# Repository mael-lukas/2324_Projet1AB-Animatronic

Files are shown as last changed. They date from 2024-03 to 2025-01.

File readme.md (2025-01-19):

# DEA : Dynamic Eagle Animatronic

Depuis la Grêce antique et le mythe du géant de bronze Talos les hommes ont toujours cherchés à créer des automates avec les moyens à leur disposition. Les animatroniques sont l'achèvement actuel de ce désir. Ce sont des poupées mécaniques plus ou moins réalistes dont le fonctionnement interne fait intervenir autant de la mécanique que de l'électronique.
Elles sont depuis plusieurs décennies et encore aujourd'hui principalement utilisées dans le domaine du divertissement au travers des parcs d'attraction, des films et des séries.

Dans le cadre d'un projet de 1ère année à l'école d'ingénieur ENSEA supervisé par [M.Papazoglou](https://github.com/mael-lukas/2324_Projet1AB_Animatronic/tree/main#supervis%C3%A9-par-mpapazoglou) nous allons créer créer une animatronique d'aigle en 10 séances de 4h. Cet animatronic sera
capable d'ouvrir et de rabattre ses ailes, d'ouvrir et de fermer ses paupières, d'ouvrir et de fermer son bec, de pivoter sa tête (optionnel). Ces mouvements seront commandés par
l'appui de différents boutons.

<table>
  <tr>
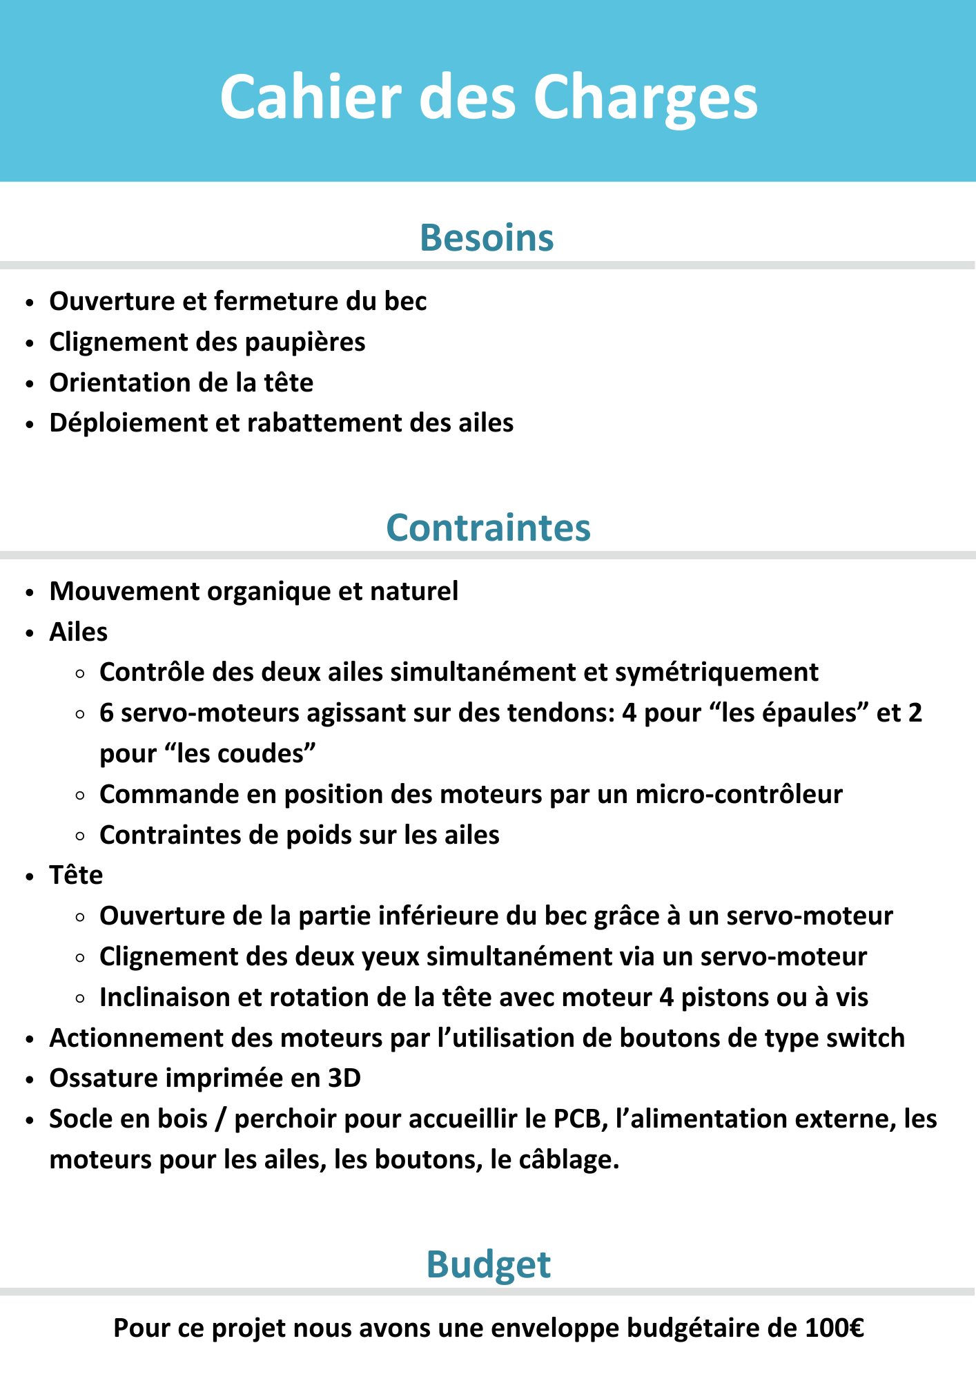
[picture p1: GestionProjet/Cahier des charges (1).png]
Cahier des charges
    <td></td>
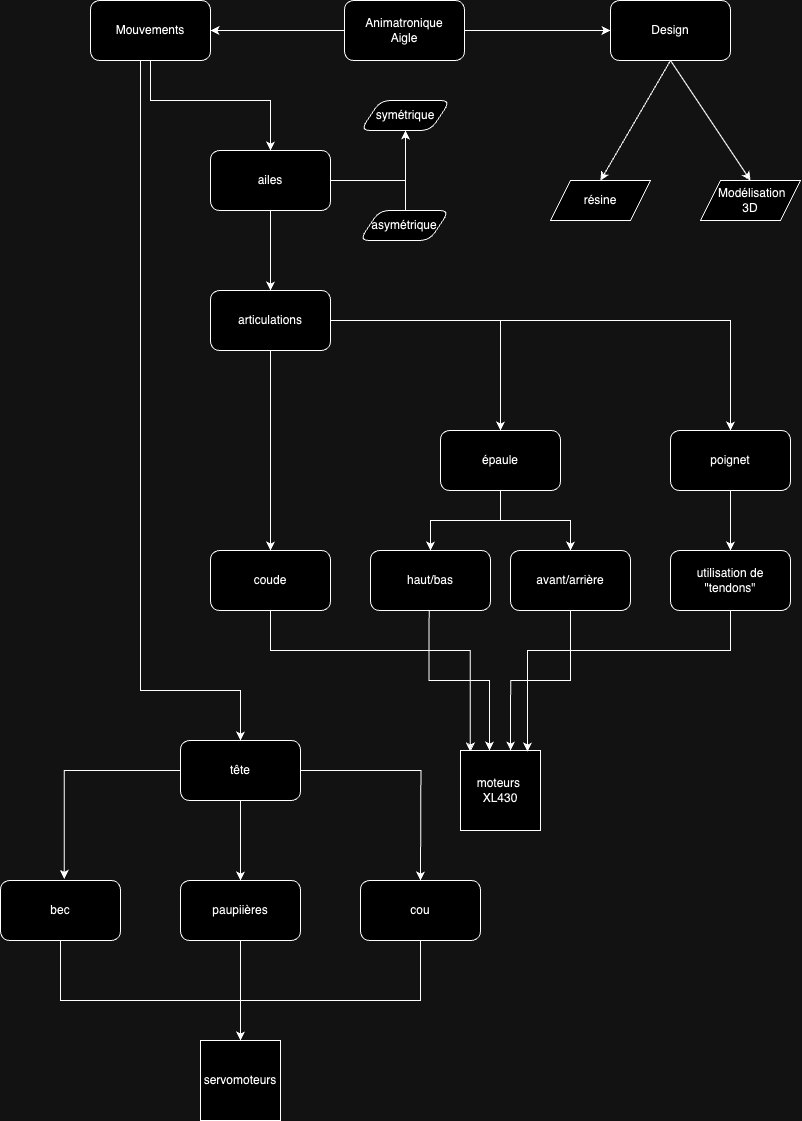
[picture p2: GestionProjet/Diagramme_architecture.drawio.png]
Diagramme d'architecture
    <td></td>
  </tr>
</table>

  [](https://github.com/mael-lukas/2324_Projet1AB_Animatronic/blob/main/GestionProjet/Cahier%20des%20charges%20(1).png)    
  [](https://github.com/mael-lukas/2324_Projet1AB_Animatronic/blob/main/GestionProjet/Diagramme_architecture.drawio.png)

# Equipe
Membres de l'équipe : 
* #### Vincent Fernandes
    * [Github](https://github.com/FernandesVincent)
    * [Linkedin](https://www.linkedin.com/in/vincent-fernandes-0981552a6/)
* #### Maël Lukas
    * [Github](https://github.com/mael-lukas)
    * [Linkedin](https://www.linkedin.com/in/mael-lukas/)
* ##### Romane Ponthieu
    * [Github](https://github.com/Romanepnth)
    * [Linkedin](https://www.linkedin.com/in/romane-ponthieu/)
* #### Marie Ceccaldi
    * [Github](https://github.com/mariececcaldi1)
    * [Linkedin](https://www.linkedin.com/in/marie-ceccaldi-887616300/)
* #### Sedrenn Labrousse
    * [Github](https://github.com/Sedrennl)
    * [Linkedin](https://www.linkedin.com/in/sédrenn-labrousse-24b2a5295/)

* #### Supervisé par Nicolas Papazoglou
    * [Github](https://github.com/DBXYD?tab=overview&from=2024-05-01&to=2024-05-29)
    * [Linkedin](https://www.linkedin.com/in/nicolas-papazoglou-38382646/?originalSubdomain=fr)

# Journal de bord

## Séance 1
   Cette séance, étant la première, nous a servit à définir notre projet au travers de la création d'une première version d'un cahier des charges et d'un diagramme d'architecture. Afin de nous organiser au mieux au vu du temps disponible à la création de ce projet nous nous sommes directement répartit différentes tâches à réaliser durant les semaines qui suivent.
   * #### modélisation 3D de l'aigle
        * [Sedrenn](https://github.com/mael-lukas/2324_Projet1AB_Animatronic/tree/main?tab=readme-ov-file#sedrenn-labrousse)
   * #### programmation des moteurs
        * [Maël](https://github.com/mael-lukas/2324_Projet1AB_Animatronic/tree/main?tab=readme-ov-file#ma%C3%ABl-lukas)
   * #### création des différents PCB
        * [Romane](https://github.com/mael-lukas/2324_Projet1AB_Animatronic/tree/main?tab=readme-ov-file#romane-ponthieu)
        * [Marie](https://github.com/mael-lukas/2324_Projet1AB_Animatronic/tree/main?tab=readme-ov-file#marie-ceccaldi)
        * [Vincent](https://github.com/mael-lukas/2324_Projet1AB_Animatronic/tree/main?tab=readme-ov-file#vincent-fernandes)

## Séance 2
   Durant cette séance nous avons affiné notre cahier des charges et notre diagramme d'architecture disponible ci-dessous:

   Nous en avons déduis la nécessité d'avoir un minimum de 2 PCB afin de réaliser notre animatronique, le principal qui contiendrait le microprocesseur ainsi que différents connectiques tandis que le secondaire incorporerai principalement en son sein tout les régulateurs de tension nécessaire à l'actionnment des moteurs. [PCB](https://github.com/mael-lukas/2324_Projet1AB_Animatronic?tab=readme-ov-file#pcb)
   Pendant ce temps, [Sedrenn](https://github.com/mael-lukas/2324_Projet1AB_Animatronic/tree/main?tab=readme-ov-file#sedrenn-labrousse) et [Maël](https://github.com/mael-lukas/2324_Projet1AB_Animatronic/tree/main?tab=readme-ov-file#ma%C3%ABl-lukas)
 se sont chargés de la commande des différents composants dont nous ne disposions pas à l'école.
   
## Séance 3
   À cette étape du projet nous avons choisis de créer un nouveau [PCB](https://github.com/mael-lukas/2324_Projet1AB_Animatronic/tree/main?tab=readme-ov-file#yeux) dans le but de pouvoir placer les LED RGB au plus proches des yeux de d'aigle. Ce PCB sera donc utilisé deux fois, un pour chaque oeil.
   En parallèle à cela, nous nous sommes penchés sur la réalisation d'un socle dont le but est d'accueillir le [PCB principal](https://github.com/mael-lukas/2324_Projet1AB_Animatronic/tree/main?tab=readme-ov-file#corps) ainsi que l'alimentation tout en permettant de poser l'aigle sur celui-ci pour y connecter l'ensemble des câbles.
   
## Séance 4
   Cette séance a permis la finalisation des schematic des 3 [PCB](https://github.com/mael-lukas/2324_Projet1AB_Animatronic?tab=readme-ov-file#pcb) crées sous Kicad et ainsi le passage à l'étape PCB editor pour les membres affectés à cette partie du projet.
   Pendant ce temps [Maël](https://github.com/mael-lukas/2324_Projet1AB_Animatronic/tree/main?tab=readme-ov-file#ma%C3%ABl-lukas) a finalisé une première version du code des petits moteurs et [Sedrenn](https://github.com/mael-lukas/2324_Projet1AB_Animatronic/tree/main?tab=readme-ov-file#sedrenn-labrousse) a trouvé le modèle 3D d'un aigle qui servira de base pour notre projet.

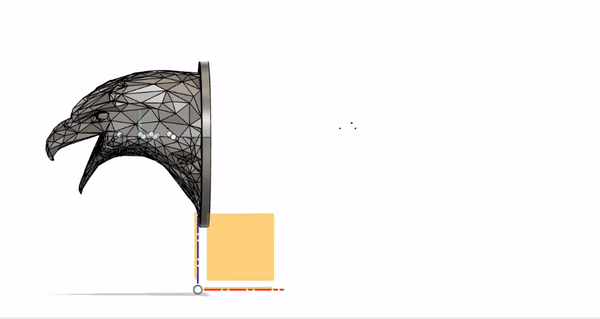
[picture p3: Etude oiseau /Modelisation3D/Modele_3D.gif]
Modèle 3D

   
## Séance 5
   Au cours de ces 4 heures M.Papazoglou a pu vérifier les 3 [PCB](https://github.com/mael-lukas/2324_Projet1AB_Animatronic?tab=readme-ov-file#pcb) et nous faire des retours pour que l'on puisse faire les dernières retouches pour ensuite pouvoir passer la commande.
   
   À ce moment là dans l'avancée du projet, toutes les réalisations énoncées à la séance 1 ont pu avancer comme il ce doit. Les pcb étaient en phase de finalisation, la programmation des moteurs a permis la commande d'un petit moteur tandis que les moteurs XL430 voyaient leur fichiers header être terminés. Finalement, la modélisation 3D...

## Séance 6
   Au cours de cette séance nous avons reçu les commandes de composants faites durant la séance 2 ainsi que les PCB qui ont donc pu être soudés par [Marie](https://github.com/mael-lukas/2324_Projet1AB_Animatronic/tree/main?tab=readme-ov-file#marie-ceccaldi) et [Romane](https://github.com/mael-lukas/2324_Projet1AB_Animatronic/tree/main?tab=readme-ov-file#romane-ponthieu) durant ces 4 heures.
   En parralèle à cela, [Sedrenn](https://github.com/mael-lukas/2324_Projet1AB_Animatronic/tree/main?tab=readme-ov-file#sedrenn-labrousse) a finalisée la première version de la tête de l'aigle en y incluant les moteurs et PCB associés:
   
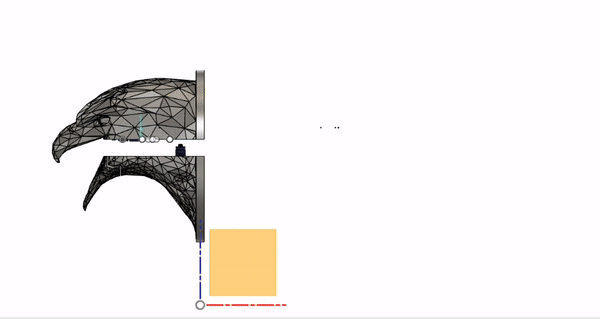
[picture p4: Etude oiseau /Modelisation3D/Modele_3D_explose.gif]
Modèle 3D finalisé

   
   [Vincent](https://github.com/mael-lukas/2324_Projet1AB_Animatronic/tree/main?tab=readme-ov-file#vincent-fernandes), quant à lui, à réalisé un premier prototype du socle réfléchit à la [Séance 3](https://github.com/mael-lukas/2324_Projet1AB_Animatronic?tab=readme-ov-file#s%C3%A9ance-3)
   
## Séance 7
   Durant cette séance, [Marie](https://github.com/mael-lukas/2324_Projet1AB_Animatronic/tree/main?tab=readme-ov-file#marie-ceccaldi) et [Romane](https://github.com/mael-lukas/2324_Projet1AB_Animatronic/tree/main?tab=readme-ov-file#romane-ponthieu) ont crées le modèle 3D d'un cache pour l'alimentation: 
   
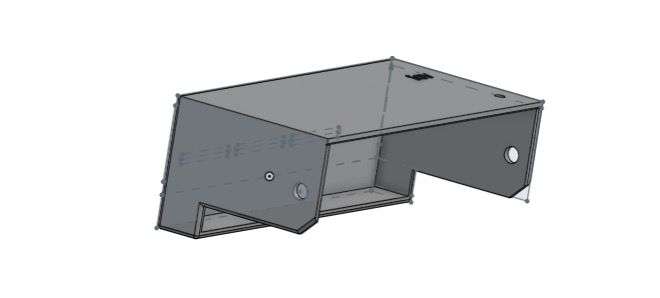
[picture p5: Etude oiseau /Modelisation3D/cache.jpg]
cache
   
   
   Pendant ce temps [Sedrenn](https://github.com/mael-lukas/2324_Projet1AB_Animatronic/tree/main?tab=readme-ov-file#sedrenn-labrousse) a imprimée une première version de la tête de l'aigle. [Vincent](https://github.com/mael-lukas/2324_Projet1AB_Animatronic/tree/main?tab=readme-ov-file#vincent-fernandes), pour sa part, a entammé la rédaction du fichier readme.md en markdown et en HTML.
   
## Séance 8
   Au cours de cette séance, [Marie](https://github.com/mael-lukas/2324_Projet1AB_Animatronic/tree/main?tab=readme-ov-file#marie-ceccaldi) et [Romane](https://github.com/mael-lukas/2324_Projet1AB_Animatronic/tree/main?tab=readme-ov-file#romane-ponthieu) ont finalisées le modèle 3D du cache entammé à la séance précédente, puis l'ont [imprimé](https://github.com/mael-lukas/2324_Projet1AB_Animatronic/blob/main/Hardware/PCB/screenshots/picture%20cache.jpg).

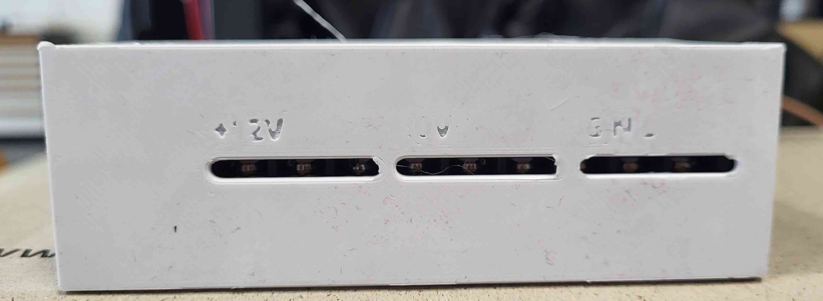
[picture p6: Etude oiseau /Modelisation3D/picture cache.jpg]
cache


Au même moment [Maël](https://github.com/mael-lukas/2324_Projet1AB_Animatronic/tree/main?tab=readme-ov-file#ma%C3%ABl-lukas) a mis au propre [l'architecture du code](https://github.com/mael-lukas/2324_Projet1AB_Animatronic?tab=readme-ov-file#code)
   
## Séance 9
  Durant cette séance nous avons réalisé une première présentation orale du projet DEA. De plus, nous avons eu les impression 3D des nouvelles et dernières versions du cache de l'alimentation ainsi que de la tête de l'aigle, toutes deux présentées ci-dessous:

<table>
  <tr>
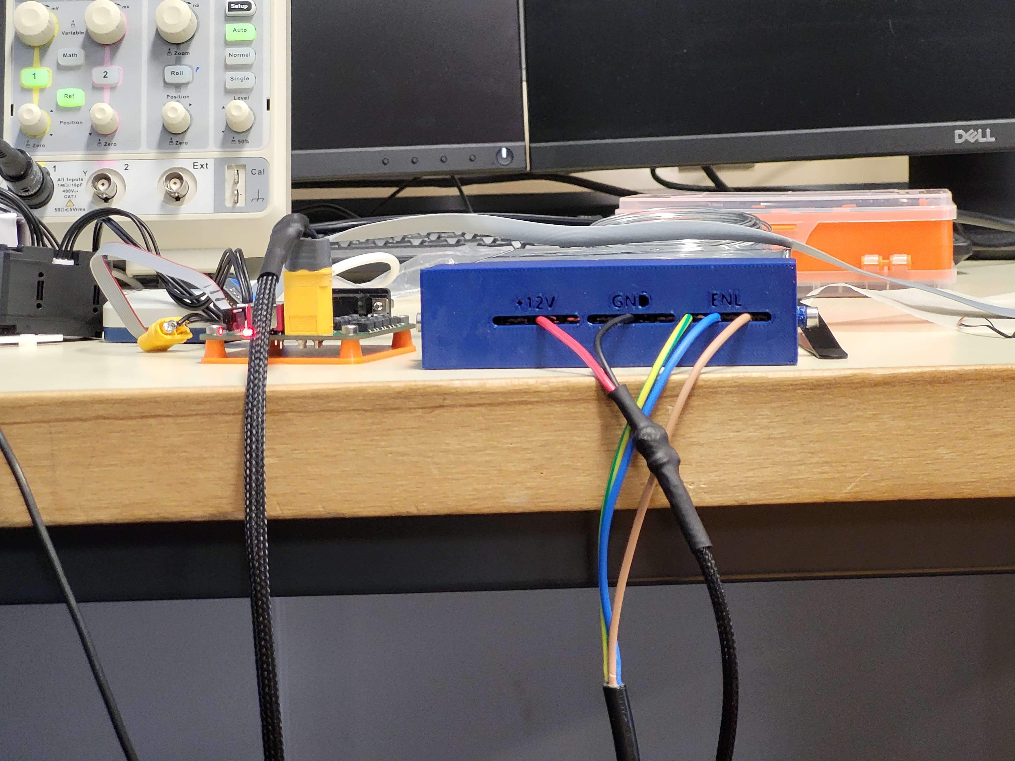
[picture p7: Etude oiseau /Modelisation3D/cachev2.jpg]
cachev2
    <td></td>
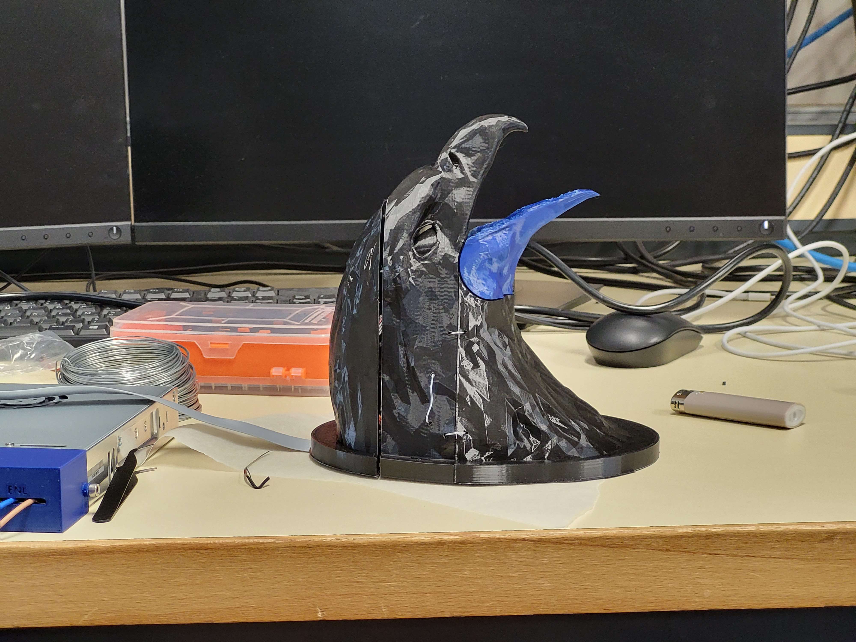
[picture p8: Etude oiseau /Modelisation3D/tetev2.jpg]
tetev2
    <td></td>
  </tr>
</table>
  
## Séance 10
   
   Au cours de cette dernière séance, nous avons assemblé la tête de l'aigle avec les différents PCB crée au cours des séance précédentes afin de permettre une ouverture et une fermeture du bec ainsi que le mouvement des paupières, ce que nous avons réussi comme en témoigne [la vidéo de démonstration du projet](https://github.com/mael-lukas/2324_Projet1AB_Animatronic/tree/main?tab=readme-ov-file#rendu-final).

   Pour faire un bilan de ce projet revenons à la base de celui-ci et comparons le à notre rendu final. Au début du projet notre objectif était de réaliser un animatronique d'aigle capable de différents mouvements de la tête ainsi que des ailes, cependant dans notre [rendu final](https://github.com/mael-lukas/2324_Projet1AB_Animatronic/tree/main?tab=readme-ov-file#rendu-final) nous avons seulement réussi à avoir la tête dans laquelle le bec et la paupière bougent. Cette différence s'explique par la difficulté liée à l'ambition d'un tel projet, en effet il y a eu plusieurs difficultés dans ce projet tel que des problèmes au niveau des PCB (problèmes de soudure, d'inversion de placement de SDA et SLC entre deux PCB et autres) ou encore sur la création de librairies pour la partie programmation et des modélisations 3D qui ont nécessitées plusieurs versions pour être opérationnelles. 
   Malgré tout cela, l'ensemble du groupe est fier et heureux d'avoir réussi à obtenir ce [résultat](https://github.com/mael-lukas/2324_Projet1AB_Animatronic/tree/main?tab=readme-ov-file#rendu-final) et ce projet ne s'arrête pas ici puisque, en effet, le groupe dans son ensemble a décidé de poursuivre ce projet durant la deuxième année de notre cursus afin de finir ce qui était prévu initialement. 
   Cependant, nous avons décidé de ne pas nous arrêter à ce que nous avions prévu et nous commencons déjà à réfléchir à des améliorations pour le DEA tel que:
   1. Un speaker dans le bec de l'aigle lié à un capteur de distance pour changer ce que l'aigle dit en fonction de la distance avec son interlocuteur.
   2. Un système permettant de contrôler les mouvements de l'aigle en fonction des mouvement de la main de l'utilisateur.
   3. Une application permettant de changer la vitesse des moteurs, la couleur des LED des yeux et de jouer certaines séquences de mouvement de l'aigle.

Ces idées ne sont encore que des réflexions et seront amennées a évoluées au cours de l'année qui arrive.
   
# Livrables
## PCB

#### Corps

Ce PCB est le PCB principal contenant le microprocesseur ainsi que les connecteurs et les bouttons utiles à l'utilisateur.

<table>
  <tr>
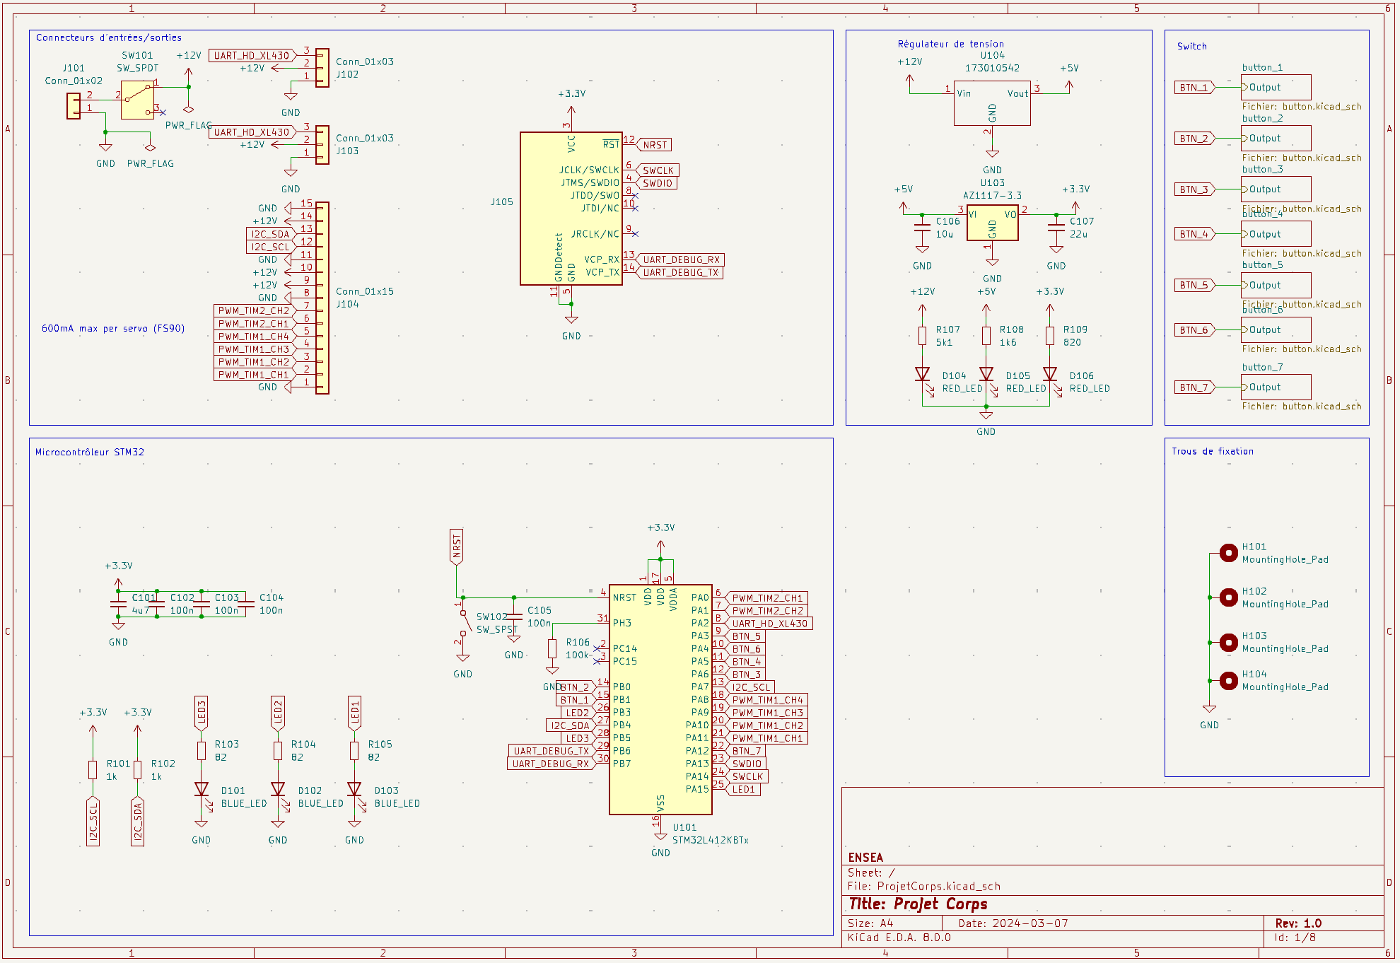
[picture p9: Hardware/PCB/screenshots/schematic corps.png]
schematic corps
    <td></td>
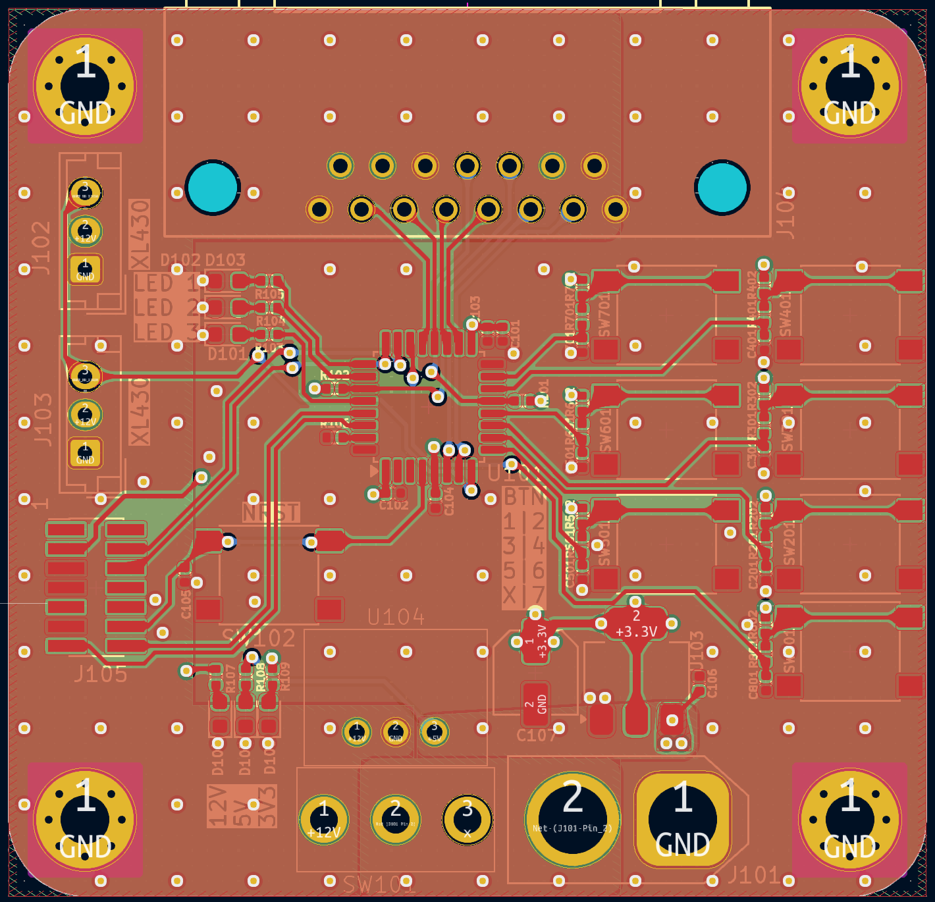
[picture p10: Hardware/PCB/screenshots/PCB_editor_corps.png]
PCB editor corps
    <td></td>
  </tr>
</table>

[Schematic](https://github.com/mael-lukas/2324_Projet1AB_Animatronic/blob/main/Hardware/PCB/screenshots/schematic%20corps.png)         
[PCB editor](https://github.com/mael-lukas/2324_Projet1AB_Animatronic/blob/main/Hardware/PCB/screenshots/PCB_editor_corps.png)

#### Tête

Ce PCB sert à réguler les tensions envoyées aux moteurs et contient également le LED driver qui permet de commander les LED présentes sur le [PCB des yeux](https://github.com/mael-lukas/2324_Projet1AB_Animatronic/tree/main?tab=readme-ov-file#yeux).

<table>
  <tr>
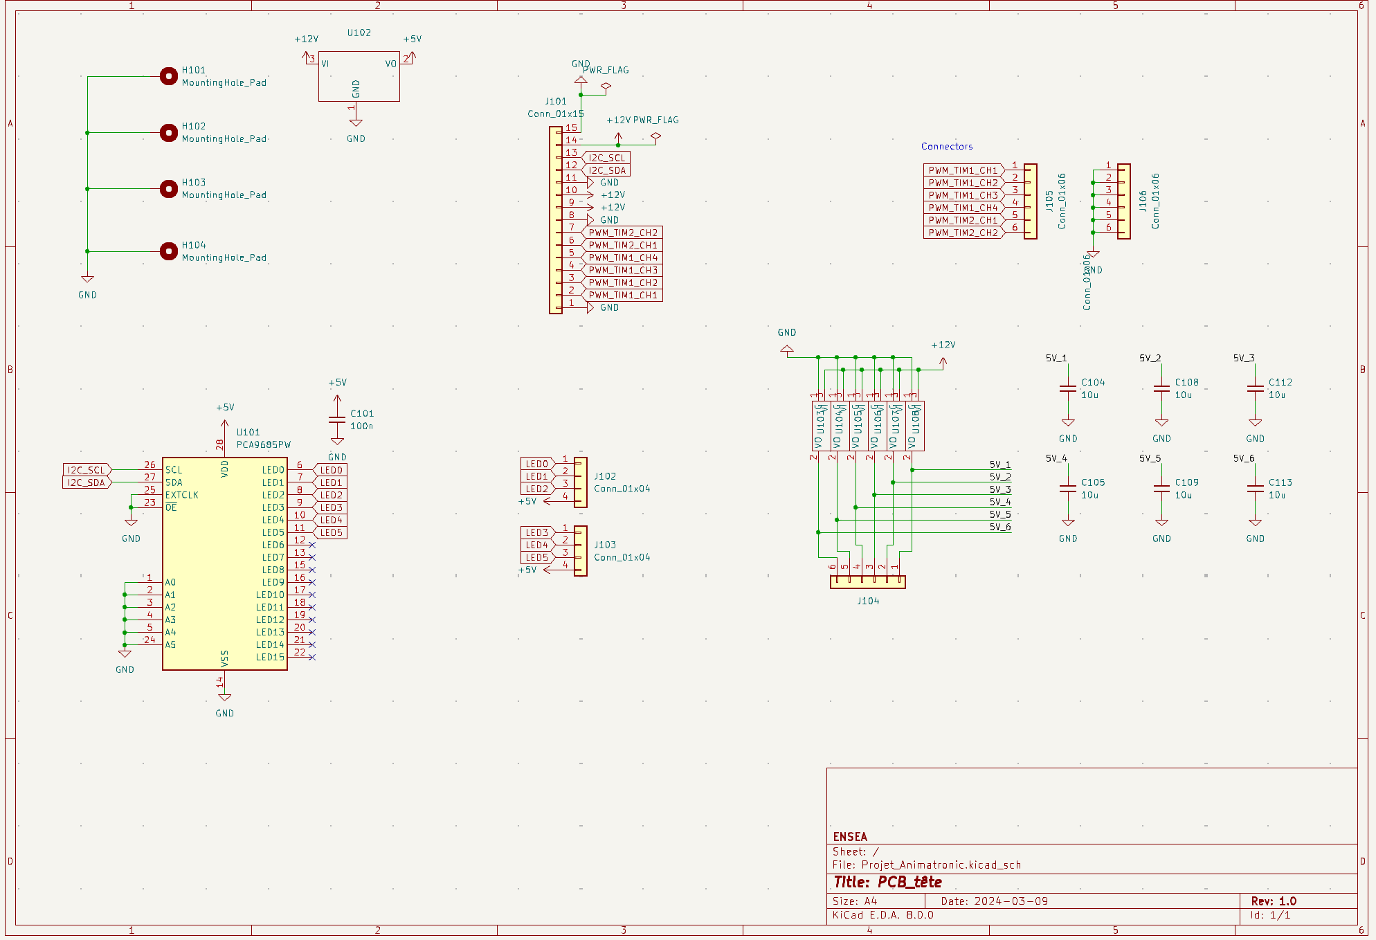
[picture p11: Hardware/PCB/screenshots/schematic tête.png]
schematic tête
    <td></td>
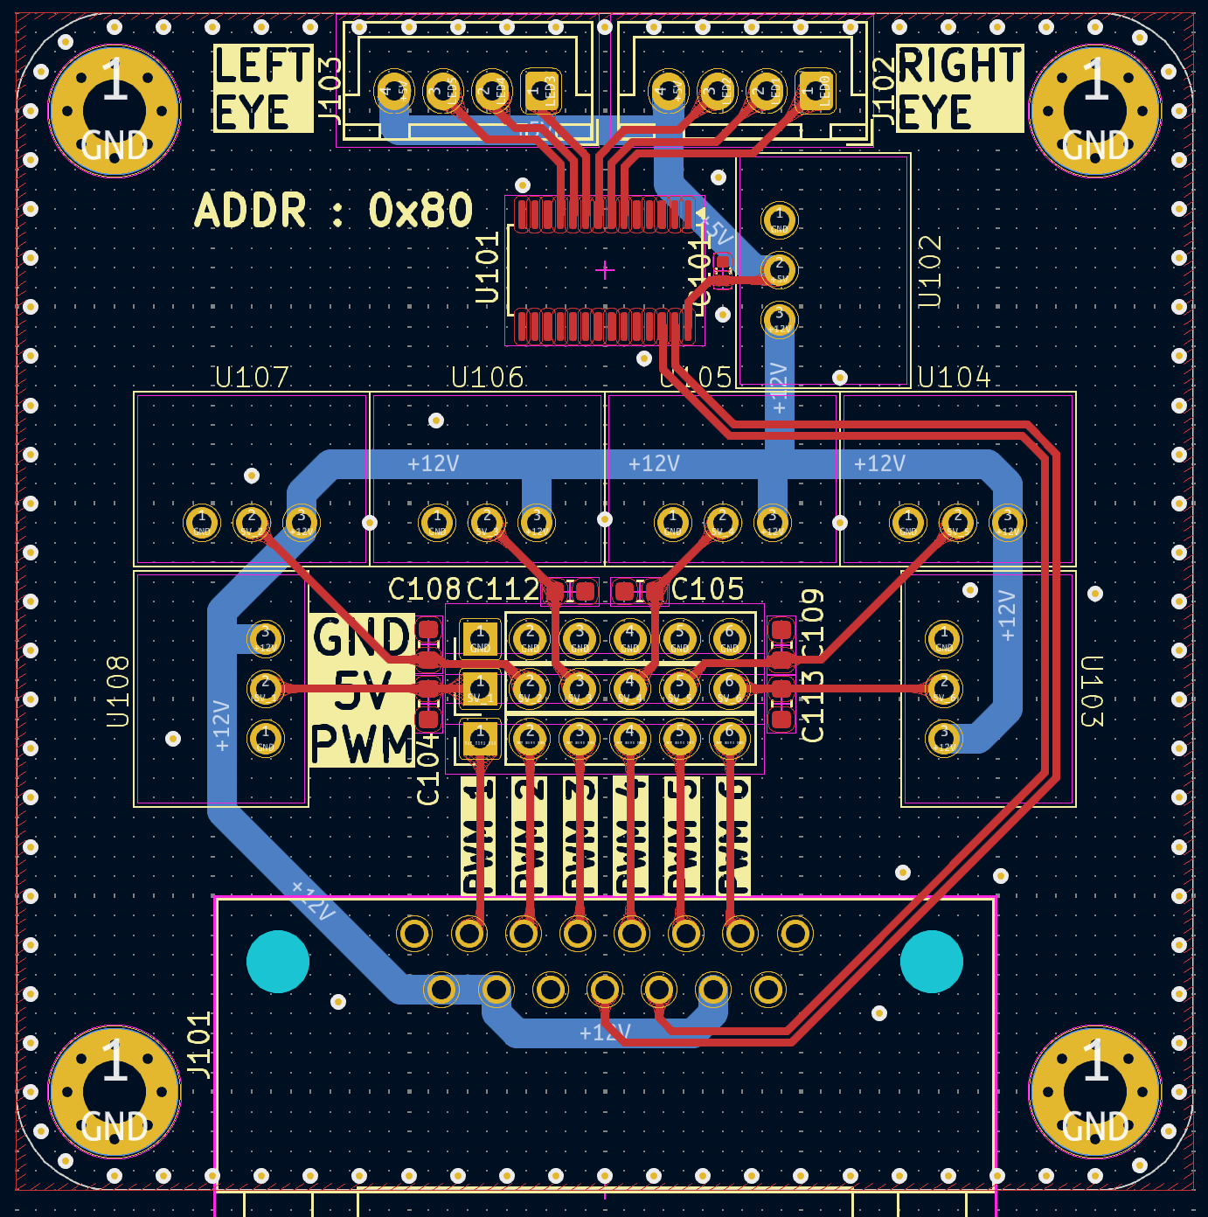
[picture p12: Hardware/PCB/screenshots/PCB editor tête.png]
PCB editor tête
    <td></td>
  </tr>
</table>

[Schematic](https://github.com/mael-lukas/2324_Projet1AB_Animatronic/blob/main/Hardware/PCB/screenshots/schematic%20t%C3%AAte.png)   
[PCB editor](https://github.com/mael-lukas/2324_Projet1AB_Animatronic/blob/main/Hardware/PCB/screenshots/PCB%20editor%20t%C3%AAte.png)

#### Yeux

Ce PCB, utilisé deux fois dans le DEA (un pour chaque oeil) à pour unique utilité de placer les LED au plus proche des yeux grâce à un connecteur qui le relie au [PCB de la tête](https://github.com/mael-lukas/2324_Projet1AB_Animatronic/tree/main?tab=readme-ov-file#t%C3%AAte).

<table>
  <tr>
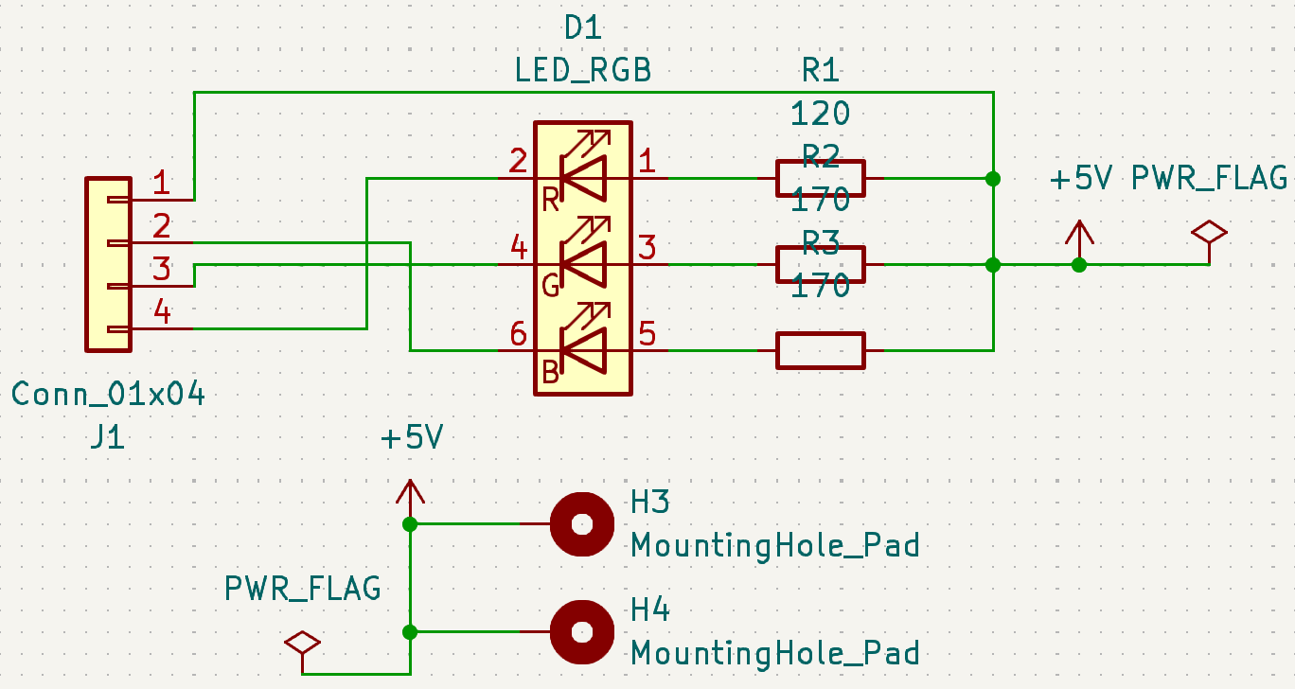
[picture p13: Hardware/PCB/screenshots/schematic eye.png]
schematic oeil
    <td></td>
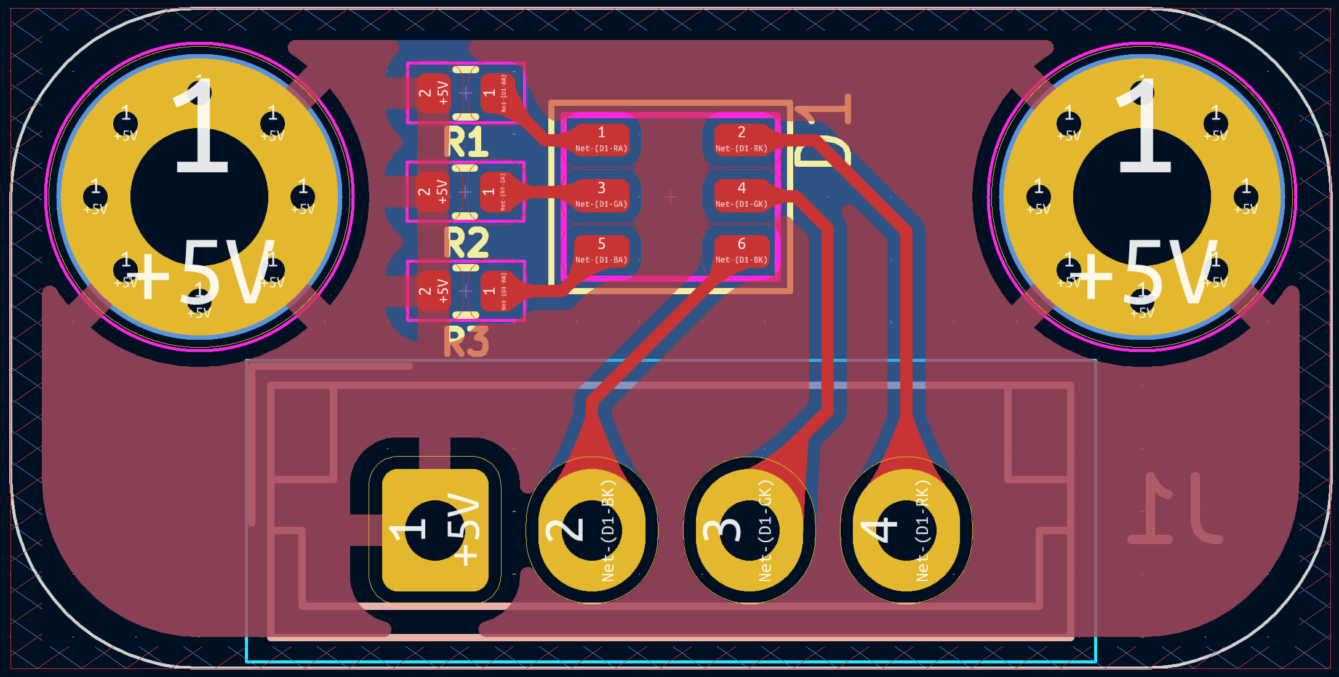
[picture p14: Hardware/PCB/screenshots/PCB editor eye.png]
PCB editor oeil
    <td></td>
  </tr>
</table>

[Schematic](https://github.com/mael-lukas/2324_Projet1AB_Animatronic/blob/main/Hardware/PCB/screenshots/schematic%20eye.png)        
[PCB editor](https://github.com/mael-lukas/2324_Projet1AB_Animatronic/blob/main/Hardware/PCB/screenshots/PCB%20editor%20eye.png)

## Code

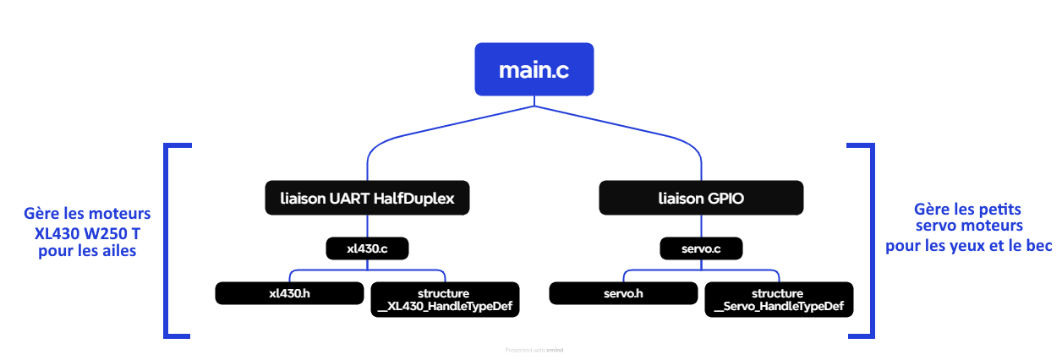
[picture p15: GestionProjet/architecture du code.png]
code


## Rendu final

video

[video en meilleure qualité (à télécharger)](https://github.com/mael-lukas/2324_Projet1AB_Animatronic/blob/main/Etude%20oiseau%20/Modelisation3D/vid.mp4)

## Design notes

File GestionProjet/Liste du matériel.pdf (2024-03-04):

## Matériel requis

Moteurs:
- 6x XL430
- 6x servo-motor

Alim:
- Alimentation 230 VA vers 12 VC
- Buck 12 V vers 5 V (un ou plusieurs si on a besoin) (173 010 542 WPMHD1100501S)
- Régulateur LDO 5 V vers 3.3 V (921-0701 AZ1117H-3.3TRE1) Composants passifs
- LEDs pour rendre compte de l’alim fonctionnelle

Microprocesseur:
- STM32L412KBT6: MCU 32 bits 80MHz LQFP-32

### 3 timers 12 sorties PWM

LEDs RGB (3584522 680MCD 1.5CD 380MCD) et LED Driver RGBA (1854074 28-TSS) pour les yeux

Connecteurs:
- Connecteur pour sonde de programmation
- Connecteurs JST moteurs:

### 2 pour le corps (3 XL430 sur chaque JST) JST 3 pins (je

pense) GND, 12V et UART

### 3 rangées de 6 pins pour la tête

Condensateurs 1 gros de 10µ et un rapide de 100n de chaque côté du bloc de 3x6
- Connecteurs entre les PCBs connecteurs 15 pins(1 fiche 1 embase corps et 1 fiche 1 embase tête)

Switchs:
- Boutons poussoirs x7 pour envoyer des infos en GPIO au microprocesseur

Composants passifs
- 2 résistances (10 kOhms) et 1 condensateur (10 nF) par condensateur

Pour le corps
Pour la tête

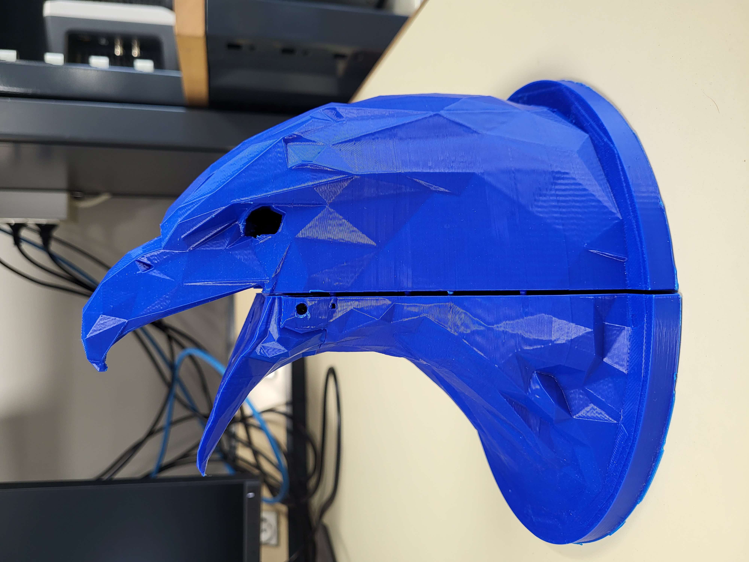
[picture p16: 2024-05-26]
Etude oiseau /Modelisation3D/tête_v1.jpg

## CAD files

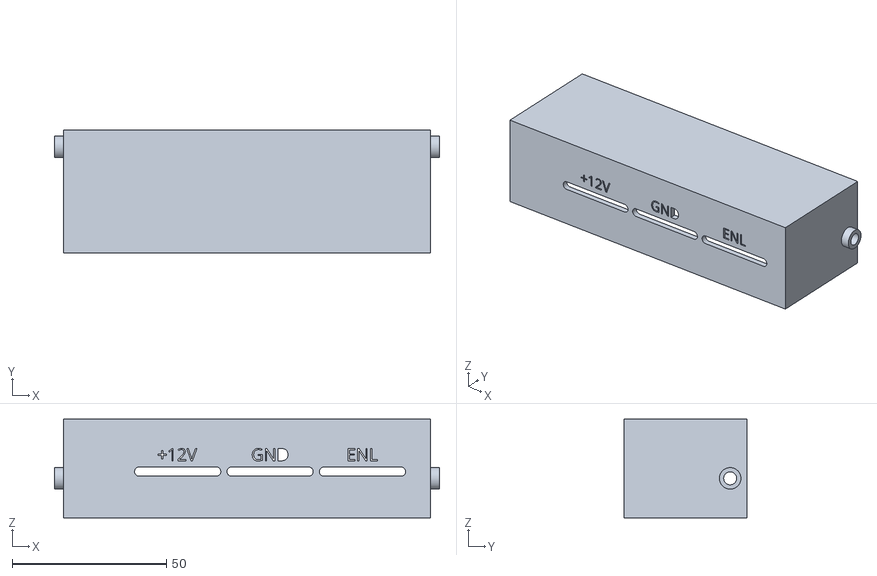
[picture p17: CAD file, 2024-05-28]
Etude oiseau /cover.stl
125.0 x 40.0 x 32.0

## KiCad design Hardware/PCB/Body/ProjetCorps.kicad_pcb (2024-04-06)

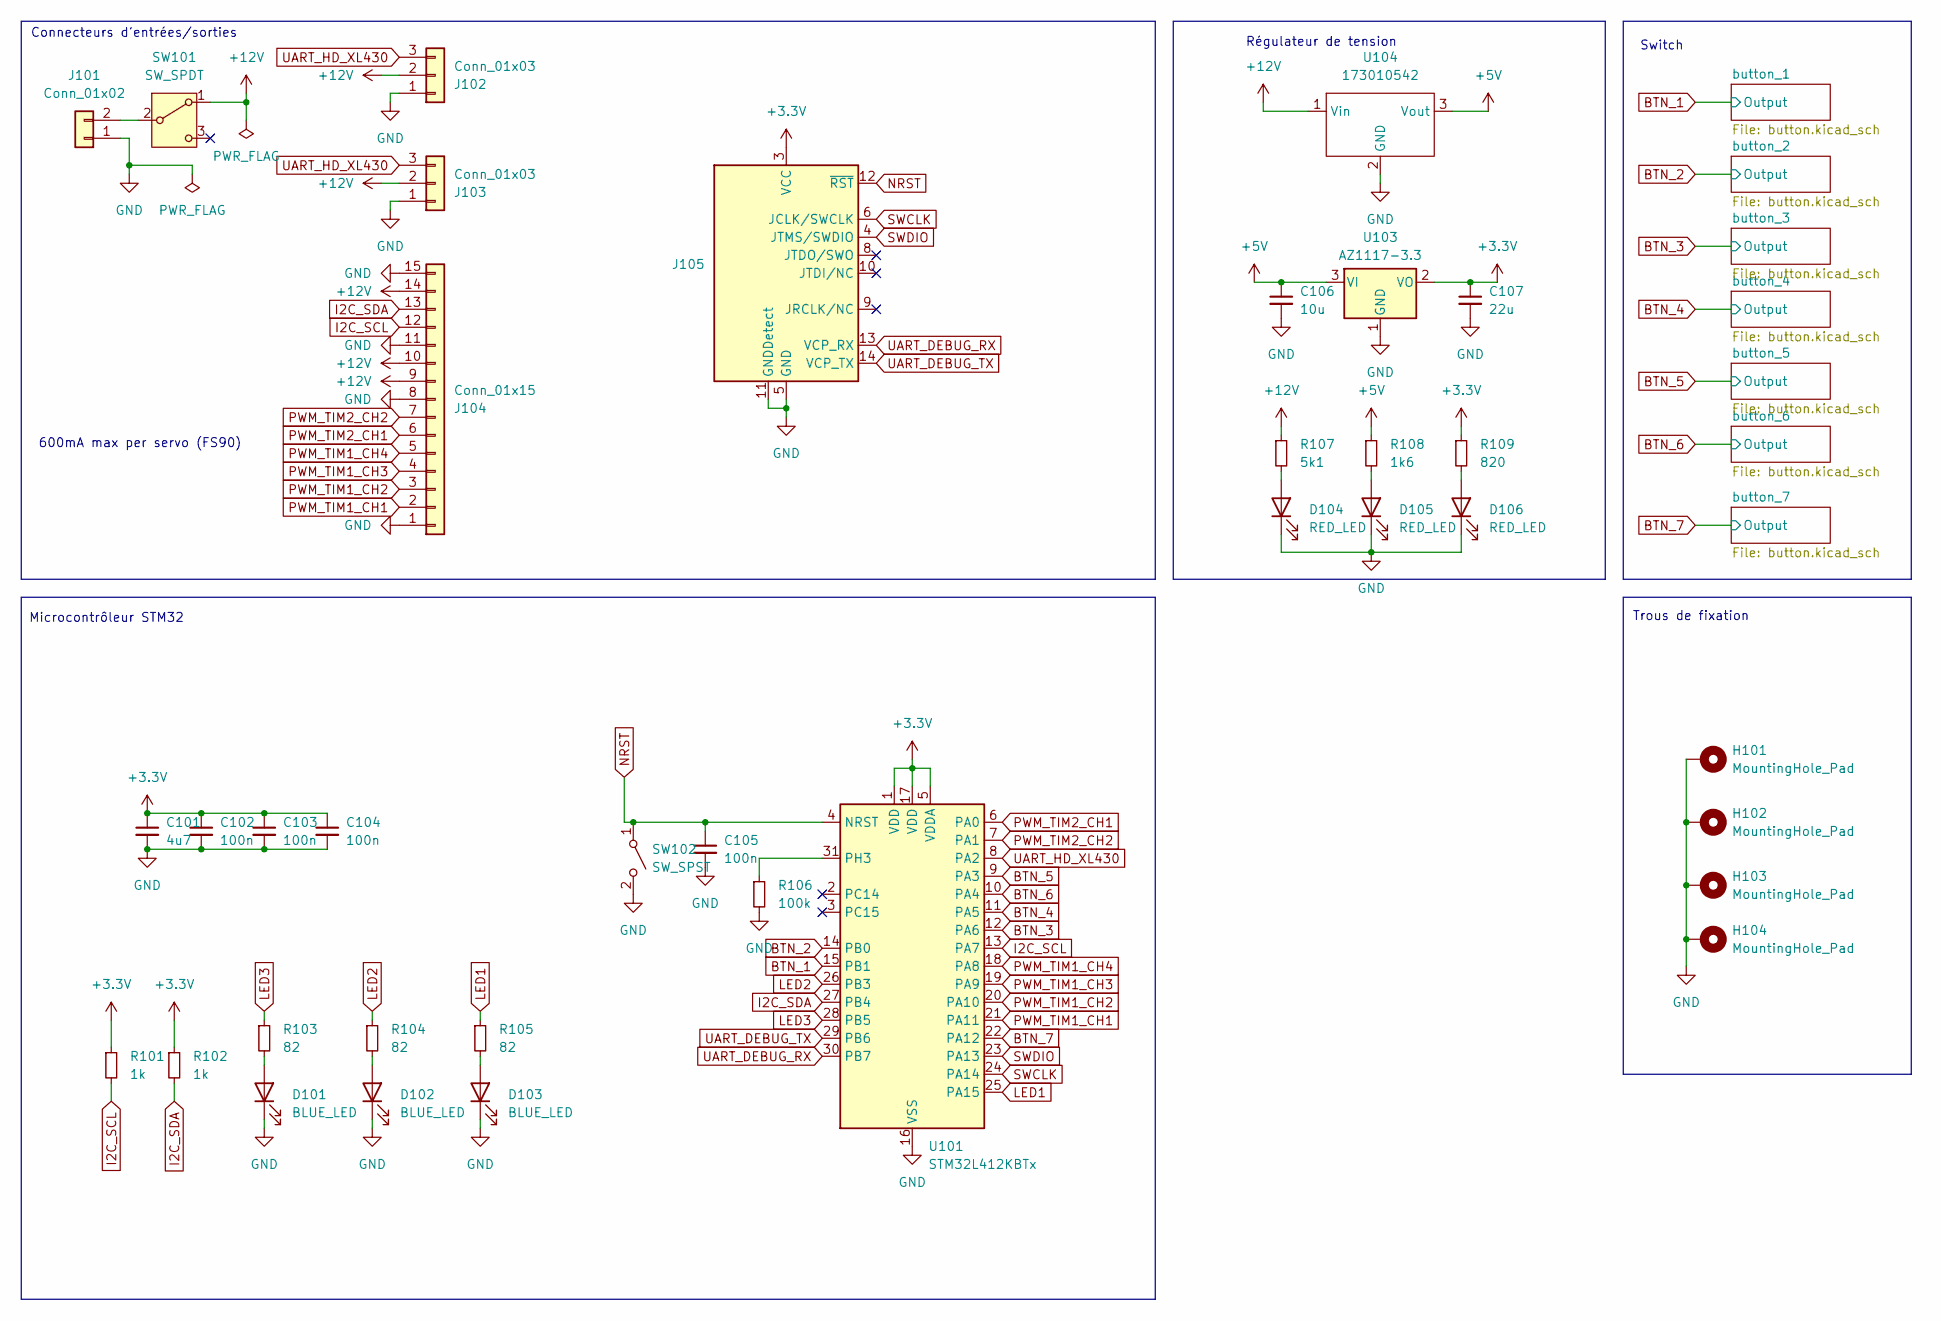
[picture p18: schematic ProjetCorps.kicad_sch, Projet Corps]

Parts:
C101: 4u7; C_0402_1005Metric
C102, C103, C104, C105: 100n; C_0402_1005Metric
C106: 10u; C_0402_1005Metric
C107: 22u; C_Elec_5x5.4
D101, D102, D103: BLUE_LED; LED_0603_1608Metric; MPN 150060BS55040
D104, D105, D106: RED_LED; LED_0603_1608Metric; MPN 150060RS55040
H101, H102, H103, H104: MountingHole_Pad; MountingHole_3.2mm_M3_Pad_Via
J101: Conn_01x02; AMASS_XT60-M_1x02_P7.20mm_Vertical
J102, J103: Conn_01x03; JST_EH_B3B-EH-A_1x03_P2.50mm_Vertical
J104: Conn_01x15; CONN15_31321_WRE; MPN 618015231421
J105: Conn_ST_STDC14; PinHeader_2x07_P1.27mm_Vertical_SMD
R101, R102: 1k; R_0402_1005Metric
R103, R104, R105: 82; R_0402_1005Metric
R106: 100k; R_0402_1005Metric
R107: 5k1; R_0402_1005Metric
R108: 1k6; R_0402_1005Metric
R109: 820; R_0402_1005Metric
SW101: SW_SPDT; 472123010111; MPN 472123010111
SW102: SW_SPST; SW_Push_1P1T_NO_6x6mm_H9.5mm
U101: STM32L412KBTx; LQFP-32_7x7mm_P0.8mm
U103: AZ1117-3.3; SOT-223-3_TabPin2; MPN AZ1117CH2-3.3TRG1
U104: 173010542

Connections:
+3.3V: C101.1, C102.1, C103.1, C104.1, C107.1, J105.3 (VCC), R101.1, R102.1, R109.1, U101.1 (VDD), U101.5 (VDDA), U101.17 (VDD), U103.2 (VO); also elsewhere on the board
+5V: C106.1, R108.1, U103.3 (VI), U104.3 (Vout)
+12V: J102.2, J103.2, J104.9, J104.10, J104.14, R107.1, SW101.1 (A), U104.1 (Vin)
BTN_1: U101.15 (PB1); also elsewhere on the board
BTN_2: U101.14 (PB0); also elsewhere on the board
BTN_3: U101.12 (PA6); also elsewhere on the board
BTN_4: U101.11 (PA5); also elsewhere on the board
BTN_5: U101.9 (PA3); also elsewhere on the board
BTN_6: U101.10 (PA4); also elsewhere on the board
BTN_7: U101.22 (PA12); also elsewhere on the board
GND: C101.2, C102.2, C103.2, C104.2, C105.2, C106.2, C107.2, D101.1 (K), D102.1 (K), D103.1 (K), D104.1 (K), D105.1 (K), D106.1 (K), H101.1, H102.1, H103.1, H104.1, J101.1, J102.1, J103.1, J104.1, J104.8, J104.11, J104.15, J105.5 (GND), J105.7 (GND), J105.11 (GNDDetect), R106.2, SW102.2 (B), U101.16 (VSS), U101.32 (VSS), U103.1 (GND), U104.2 (GND); also elsewhere on the board
I2C_SCL: J104.12, R101.2, U101.13 (PA7)
I2C_SDA: J104.13, R102.2, U101.27 (PB4)
LED1: R105.1, U101.25 (PA15)
LED2: R104.1, U101.26 (PB3)
LED3: R103.1, U101.28 (PB5)
NRST: C105.1, J105.12 (~RST), SW102.1 (A), U101.4 (NRST)
unnamed: D101.2 (A), R103.2
unnamed: D102.2 (A), R104.2
unnamed: D103.2 (A), R105.2
unnamed: D104.2 (A), R107.2
unnamed: D105.2 (A), R108.2
unnamed: D106.2 (A), R109.2
unnamed: J101.2, SW101.2 (B)
unnamed: R106.1, U101.31 (PH3)
PWM_TIM1_CH1: J104.2, U101.21 (PA11)
PWM_TIM1_CH2: J104.3, U101.20 (PA10)
PWM_TIM1_CH3: J104.4, U101.19 (PA9)
PWM_TIM1_CH4: J104.5, U101.18 (PA8)
PWM_TIM2_CH1: J104.6, U101.6 (PA0)
PWM_TIM2_CH2: J104.7, U101.7 (PA1)
SWCLK: J105.6 (JCLK/SWCLK), U101.24 (PA14)
SWDIO: J105.4 (JTMS/SWDIO), U101.23 (PA13)
UART_DEBUG_RX: J105.13 (VCP_RX), U101.30 (PB7)
UART_DEBUG_TX: J105.14 (VCP_TX), U101.29 (PB6)
UART_HD_XL430: J102.3, J103.3, U101.8 (PA2)

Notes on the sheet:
600mA max per servo (FS90)
Microcontrôleur STM32
Switch
Connecteurs d'entrées/sorties
Trous de fixation
Régulateur de tension

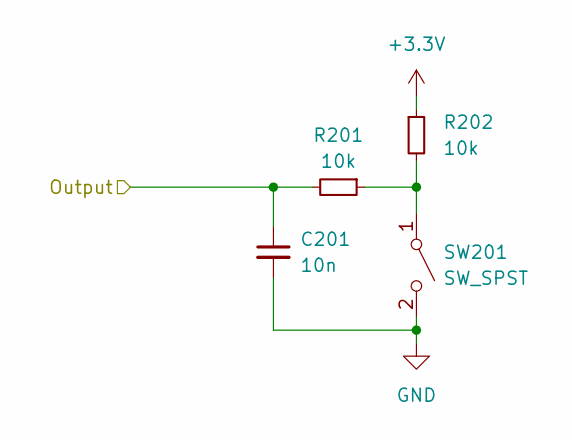
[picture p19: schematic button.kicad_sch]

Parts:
C201: 10n; C_0402_1005Metric
R201, R202: 10k; R_0402_1005Metric
SW201: SW_SPST; SW_Push_1P1T_NO_6x6mm_H9.5mm

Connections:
+3.3V: R202.1; also elsewhere on the board
BTN_6: C201.1, R201.2; also elsewhere on the board
GND: C201.2, SW201.2 (B); also elsewhere on the board
unnamed: R201.1, R202.2, SW201.1 (A)

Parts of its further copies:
C301, C401, C501, C601, C701, C801: 10n; C_0402_1005Metric
R301, R302, R401, R402, R501, R502, R601, R602, R701, R702, R801, R802: 10k; R_0402_1005Metric
SW301, SW401, SW501, SW601, SW701, SW801: SW_SPST; SW_Push_1P1T_NO_6x6mm_H9.5mm

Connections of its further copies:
+3.3V: R302.1, R402.1, R502.1, R602.1, R702.1, R802.1; also elsewhere on the board
BTN_1: C701.1, R701.2; also elsewhere on the board
BTN_2: C401.1, R401.2; also elsewhere on the board
BTN_3: C601.1, R601.2; also elsewhere on the board
BTN_4: C301.1, R301.2; also elsewhere on the board
BTN_5: C501.1, R501.2; also elsewhere on the board
BTN_7: C801.1, R801.2; also elsewhere on the board
GND: C301.2, C401.2, C501.2, C601.2, C701.2, C801.2, SW301.2 (B), SW401.2 (B), SW501.2 (B), SW601.2 (B), SW701.2 (B), SW801.2 (B); also elsewhere on the board
unnamed: R301.1, R302.2, SW301.1 (A)
unnamed: R401.1, R402.2, SW401.1 (A)
unnamed: R501.1, R502.2, SW501.1 (A)
unnamed: R601.1, R602.2, SW601.1 (A)
unnamed: R701.1, R702.2, SW701.1 (A)
unnamed: R801.1, R802.2, SW801.1 (A)

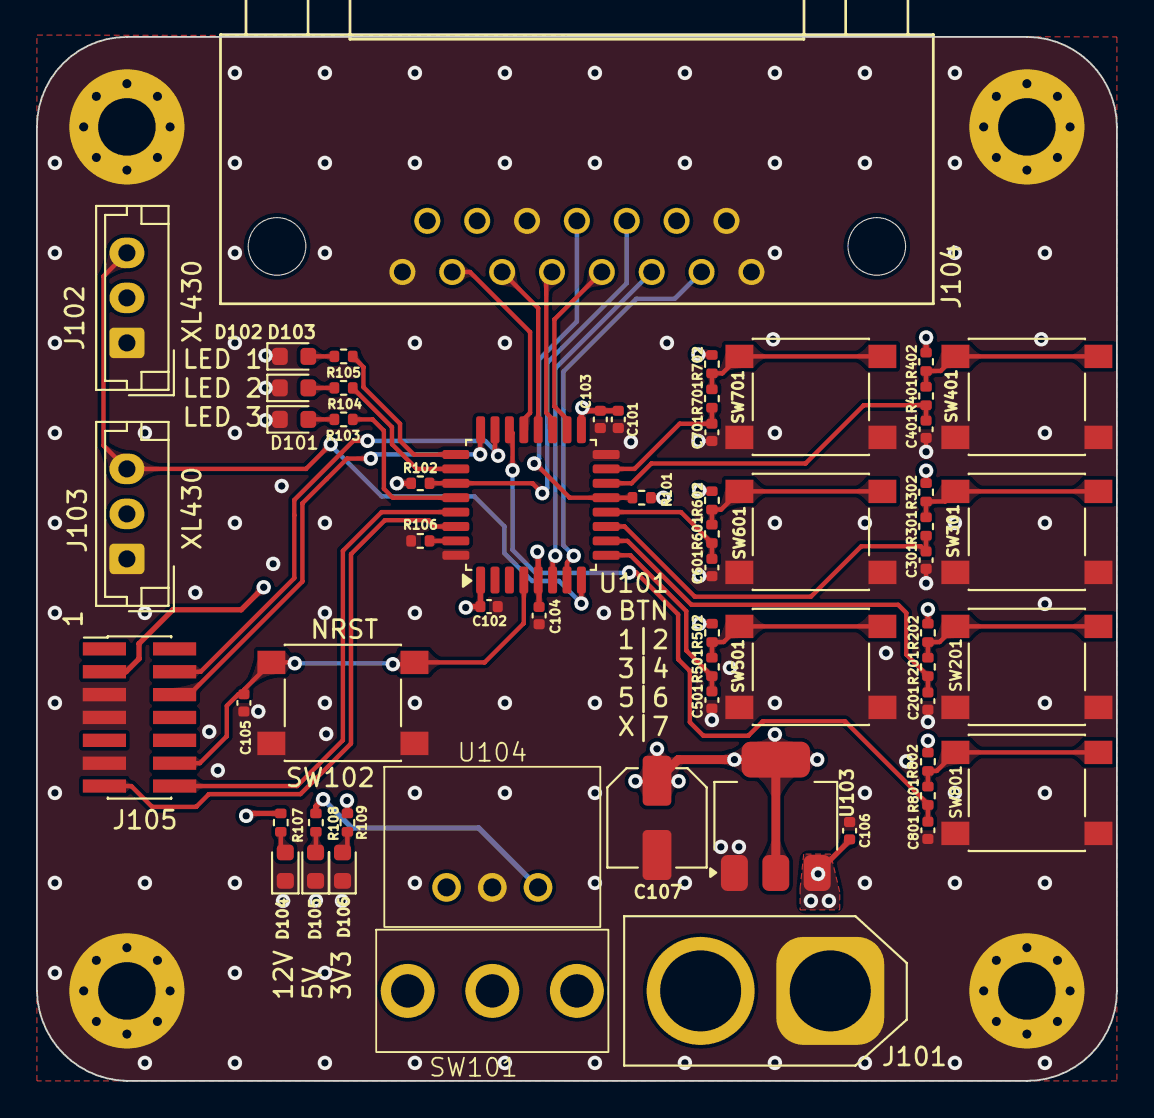
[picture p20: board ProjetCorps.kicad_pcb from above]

Board: 4 copper layers, 60.0 x 58.0 mm, 64 parts (0 on the bottom side), 43 nets.

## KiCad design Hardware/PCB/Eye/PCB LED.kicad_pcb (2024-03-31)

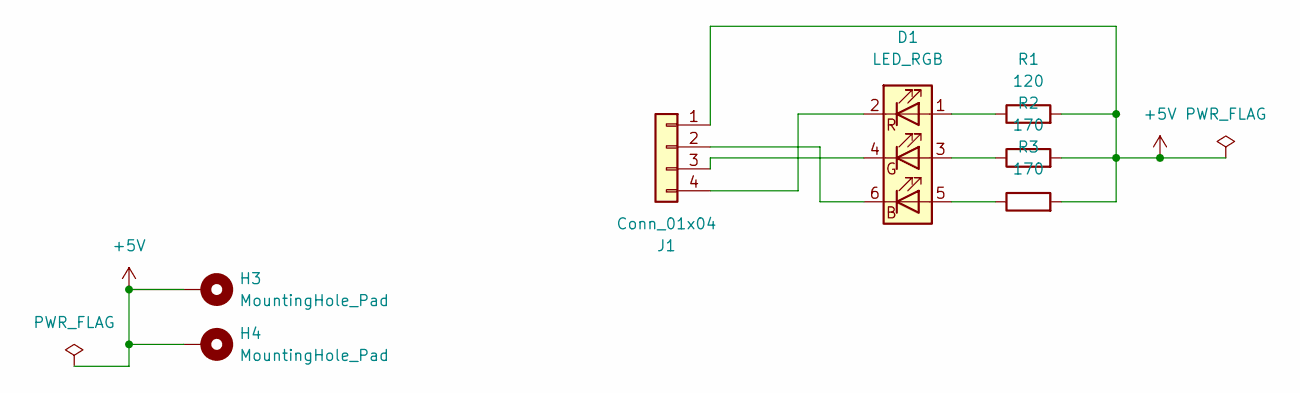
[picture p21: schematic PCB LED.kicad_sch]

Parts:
D1: LED_RGB; LED RGB
H3, H4: MountingHole_Pad; MountingHole_2.2mm_M2_Pad_Via
J1: Conn_01x04; JST_EH_B4B-EH-A_1x04_P2.50mm_Vertical
R1: 120; R_0402_1005Metric
R2, R3: 170; R_0402_1005Metric

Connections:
+5V: H3.1, H4.1, J1.1, R1.2, R2.2, R3.2
unnamed: D1.5 (BA), R3.1
unnamed: D1.6 (BK), J1.2
unnamed: D1.3 (GA), R2.1
unnamed: D1.4 (GK), J1.3
unnamed: D1.1 (RA), R1.1
unnamed: D1.2 (RK), J1.4

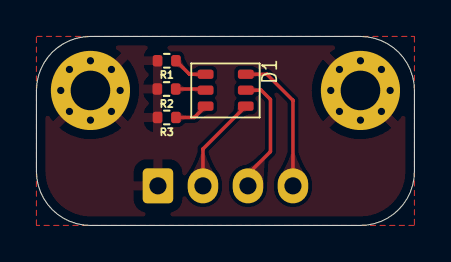
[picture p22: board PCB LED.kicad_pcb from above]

Board: 2 copper layers, 21.0 x 10.5 mm, 7 parts (1 on the bottom side), 7 nets.

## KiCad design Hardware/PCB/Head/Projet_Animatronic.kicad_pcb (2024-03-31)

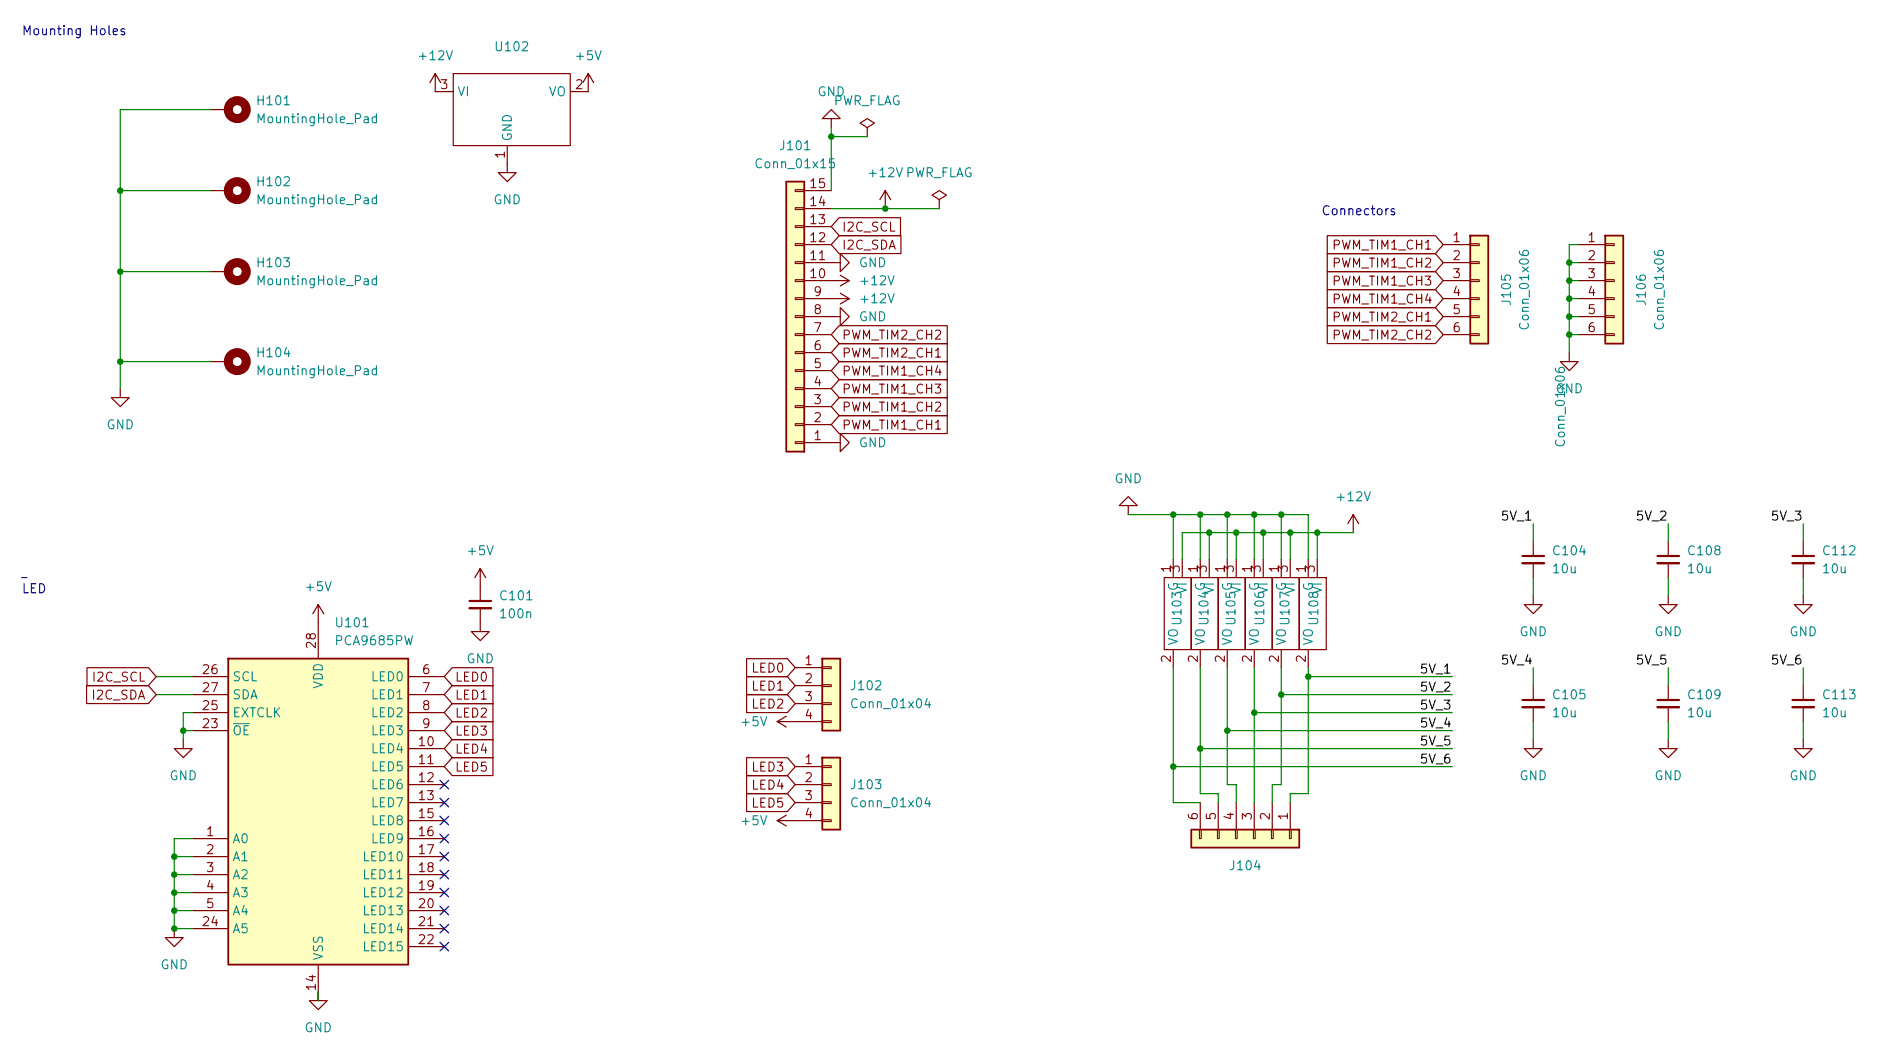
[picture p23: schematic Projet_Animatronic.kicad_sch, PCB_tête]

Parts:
C101: 100n; C_0402_1005Metric
C104, C105, C108, C109, C112, C113: 10u; C_0603_1608Metric
H101, H102, H103, H104: MountingHole_Pad; MountingHole_3.2mm_M3_Pad_Via
J101: Conn_01x15; CONN15_31321_WRE; MPN 618015231321
J102, J103: Conn_01x04; JST_XH_B4B-XH-A_1x04_P2.50mm_Vertical
J104, J105, J106: Conn_01x06; PinHeader_1x06_P2.54mm_Vertical
U101: PCA9685PW; TSSOP-28_4.4x9.7mm_P0.65mm
U102, U103, U104, U105, U106, U107, U108: 173010542

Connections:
+5V: C101.1, J102.4, J103.4, U101.28 (VDD), U102.2 (VO)
+12V: J101.9, J101.10, J101.14, U102.3 (VI), U103.3 (VI), U104.3 (VI), U105.3 (VI), U106.3 (VI), U107.3 (VI), U108.3 (VI)
/5V_1: C104.1, J104.1, U108.2 (VO)
/5V_2: C108.1, J104.2, U107.2 (VO)
/5V_3: C112.1, J104.3, U106.2 (VO)
/5V_4: C105.1, J104.4, U105.2 (VO)
/5V_5: C109.1, J104.5, U104.2 (VO)
/5V_6: C113.1, J104.6, U103.2 (VO)
GND: C101.2, C104.2, C105.2, C108.2, C109.2, C112.2, C113.2, H101.1, H102.1, H103.1, H104.1, J101.1, J101.8, J101.11, J101.15, J106.1, J106.2, J106.3, J106.4, J106.5, J106.6, U101.1 (A0), U101.2 (A1), U101.3 (A2), U101.4 (A3), U101.5 (A4), U101.14 (VSS), U101.23 (~OE), U101.24 (A5), U101.25 (EXTCLK), U102.1 (GND), U103.1 (G), U104.1 (G), U105.1 (G), U106.1 (G), U107.1 (G), U108.1 (G)
I2C_SCL: J101.13, U101.26 (SCL)
I2C_SDA: J101.12, U101.27 (SDA)
LED0: J102.1, U101.6 (LED0)
LED1: J102.2, U101.7 (LED1)
LED2: J102.3, U101.8 (LED2)
LED3: J103.1, U101.9 (LED3)
LED4: J103.2, U101.10 (LED4)
LED5: J103.3, U101.11 (LED5)
PWM_TIM1_CH1: J101.2, J105.1
PWM_TIM1_CH2: J101.3, J105.2
PWM_TIM1_CH3: J101.4, J105.3
PWM_TIM1_CH4: J101.5, J105.4
PWM_TIM2_CH1: J101.6, J105.5
PWM_TIM2_CH2: J101.7, J105.6

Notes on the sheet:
LED
Connectors
Mounting Holes

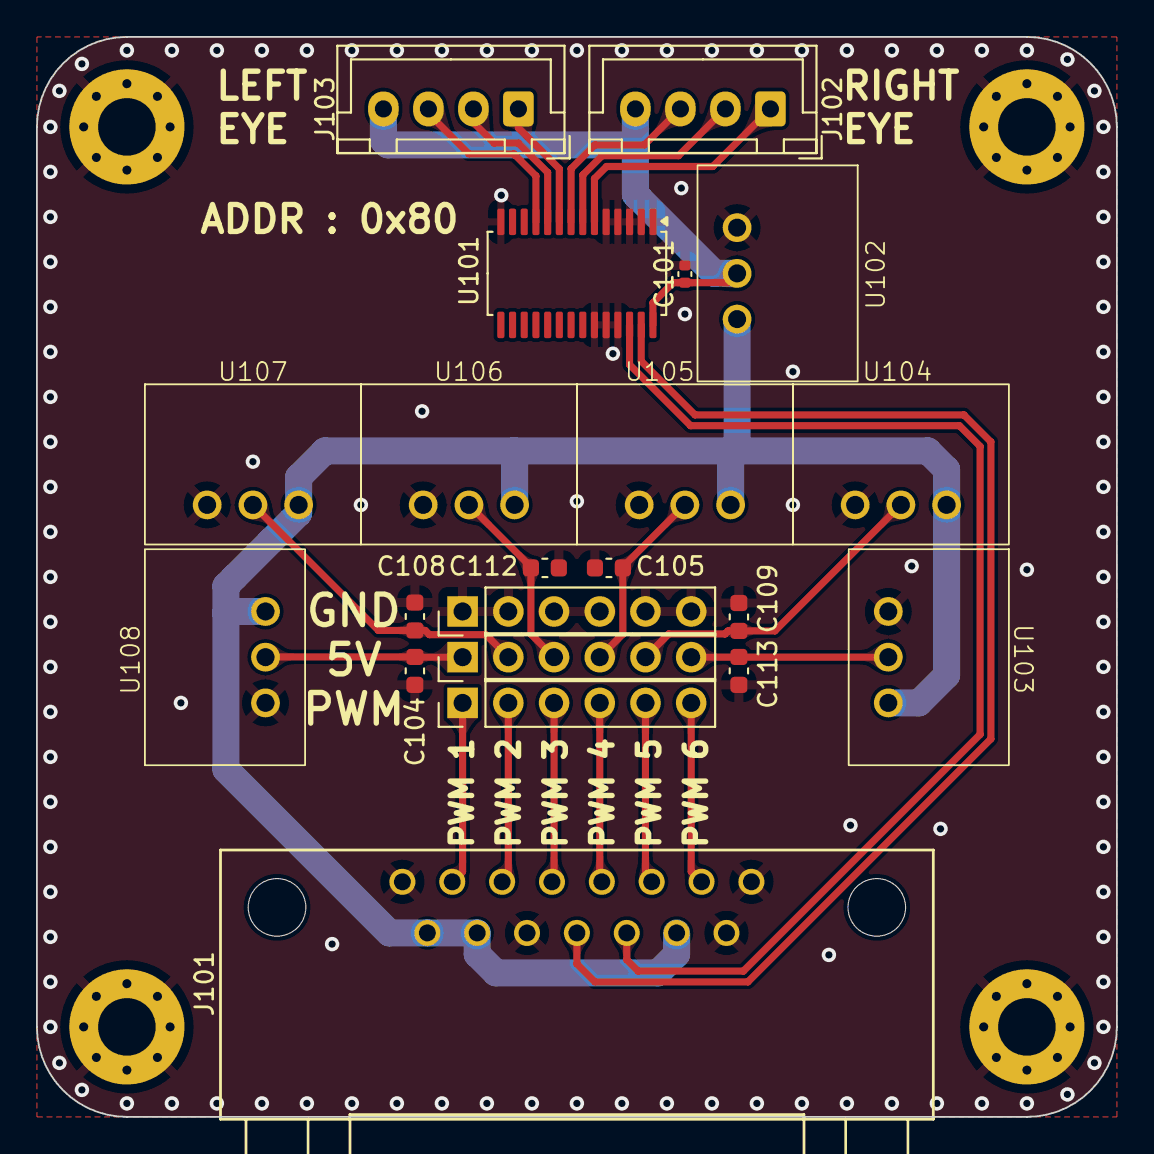
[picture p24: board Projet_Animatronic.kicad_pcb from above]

Board: 2 copper layers, 60.0 x 60.0 mm, 25 parts (0 on the bottom side), 23 nets.

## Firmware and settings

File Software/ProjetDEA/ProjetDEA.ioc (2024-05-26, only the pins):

Mcu.UserName=STM32L412KBTx
PA0-CK_IN.Signal=S_TIM2_CH1
PA1.Signal=S_TIM2_CH2
PA10.Signal=S_TIM1_CH3
PA11.Signal=S_TIM1_CH4
PA12.GPIO_Label=BTN_7_M
PA12.Signal=GPXTI12
PA2.Signal=USART2_TX
PA3.GPIO_Label=BTN_5
PA3.Signal=GPXTI3
PA4.GPIO_Label=BTN_6_M
PA4.Signal=GPXTI4
PA5.GPIO_Label=BTN_4
PA5.Signal=GPXTI5
PA6.GPIO_Label=BTN_3
PA6.Signal=GPXTI6
PA7.Signal=I2C3_SCL
PA8.Signal=S_TIM1_CH1
PA9.Signal=S_TIM1_CH2
PB0.GPIO_Label=BTN_2
PB0.Signal=GPXTI0
PB1.GPIO_Label=BTN_1
PB1.Signal=GPXTI1
PB5.GPIO_Label=LED3
PB5.Signal=GPIO_Output
PB6.Signal=USART1_TX
PB7.Signal=USART1_RX

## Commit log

2024-02-26 Cahier des charges fonctionnel en cours
2024-03-04 Datasheet buck
2024-03-04 datasheet STM32L412KBT6
2024-03-04 LED Driver
2024-03-04 Régulateur de tension
2024-03-11 schémas et empreintes composants PCB
    618015231421 == WR-DSUB 10.30 mm Male Angled PCB Connector w. Hex Screw
    5988G10313F == Dialight LED RGB
    618015231321 == WR-DSUB 10.30 mm Female Angled PCB Connector w. Hex Screw
2024-03-11 schematic 1st version mb
    [ProjetCorps.kicad_pcb, ProjetCorps.kicad_sch, button.kicad_sch]
2024-03-18 changement pcb tete
    [ProjetCorps.kicad_pcb, ProjetCorps.kicad_sch, Projet_Animatronic.kicad_pcb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]
2024-03-18 change i2c addr led driver conf
    [Projet_Animatronic.kicad_pcb, Projet_Animatronic.kicad_sch]
2024-03-25 revue PCB
    [ProjetCorps.kicad_pcb, ProjetCorps.kicad_sch, button.kicad_sch]
2024-03-26 update pcb
    [PCB LED.kicad_pcb, PCB LED.kicad_sch, ProjetCorps.kicad_pcb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]
2024-03-28 update head pcb
    [Projet_Animatronic.kicad_pcb, Projet_Animatronic.kicad_sch, untitled.kicad_sch]
2024-03-28 update eye
    [PCB LED.kicad_pcb, PCB LED.kicad_sch]
2024-03-31 export gerbers
    [PCB LED-B_Cu.gbr, PCB LED-B_Mask.gbr, PCB LED-B_Paste.gbr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]
2024-04-06 correct mistake body pcb
    [ProjetCorps-B_Cu.gbr, ProjetCorps-B_Mask.gbr, ProjetCorps-B_Paste.gbr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]
2024-04-29 cahier des charges maj
2024-05-26 code pour les mini servo fini
2024-05-26 maj cahier des charges
2024-05-28 cache de l'alim
    [cover.stl]
2024-05-28 modélisation 3d tête de l'oiseau
2024-05-29 arrangement des pj
